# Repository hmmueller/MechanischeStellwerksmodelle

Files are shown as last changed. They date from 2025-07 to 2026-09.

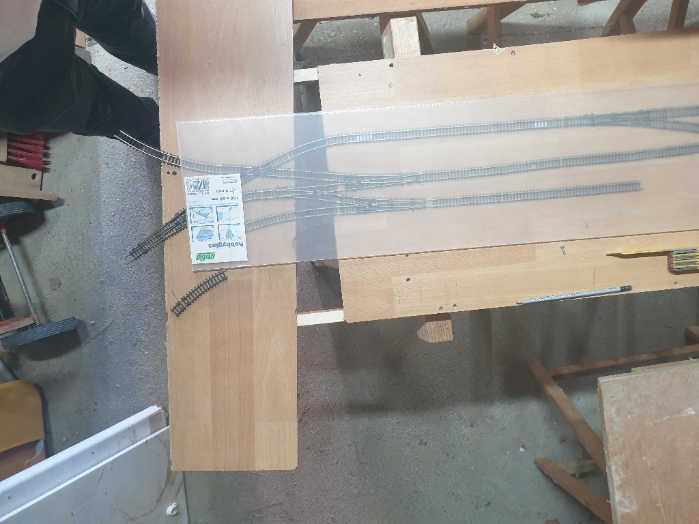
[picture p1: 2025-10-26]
Projektdokumente/20250831.KreuzdorfGleiseAusgelegt.jpeg

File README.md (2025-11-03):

# Mechanische Stellwerksmodelle

Pläne für nachempfundene Mechaniken von Stellwerken

* Die CAD-Dateien (.MOD-Dateien) sind mit BeckerCAD 11 2D gezeichnet.
* Die CNC-Pfad-Zeichnungen (P-, S- und V-Blätter) sind Input für den [PathDxf2GCode-Generator](https://github.com/hmmueller/PathDxf2GCode).

Plans for functional models of mechanical railway interlockings

* The CAD files (.MOD files) are created with BeckerCAD 11 2D.
* The CNC path drawings (P, S and V files) are input for the gcode generator [PathDxf2GCode](https://github.com/hmmueller/PathDxf2GCode).

Shield: [][cc-by]

This work is licensed under a
[Creative Commons Attribution 4.0 International License][cc-by].

[][cc-by]

[cc-by]: http://creativecommons.org/licenses/by/4.0/
[cc-by-image]: https://i.creativecommons.org/l/by/4.0/88x31.png
[cc-by-shield]: https://img.shields.io/badge/License-CC%20BY%204.0-lightgrey.svg

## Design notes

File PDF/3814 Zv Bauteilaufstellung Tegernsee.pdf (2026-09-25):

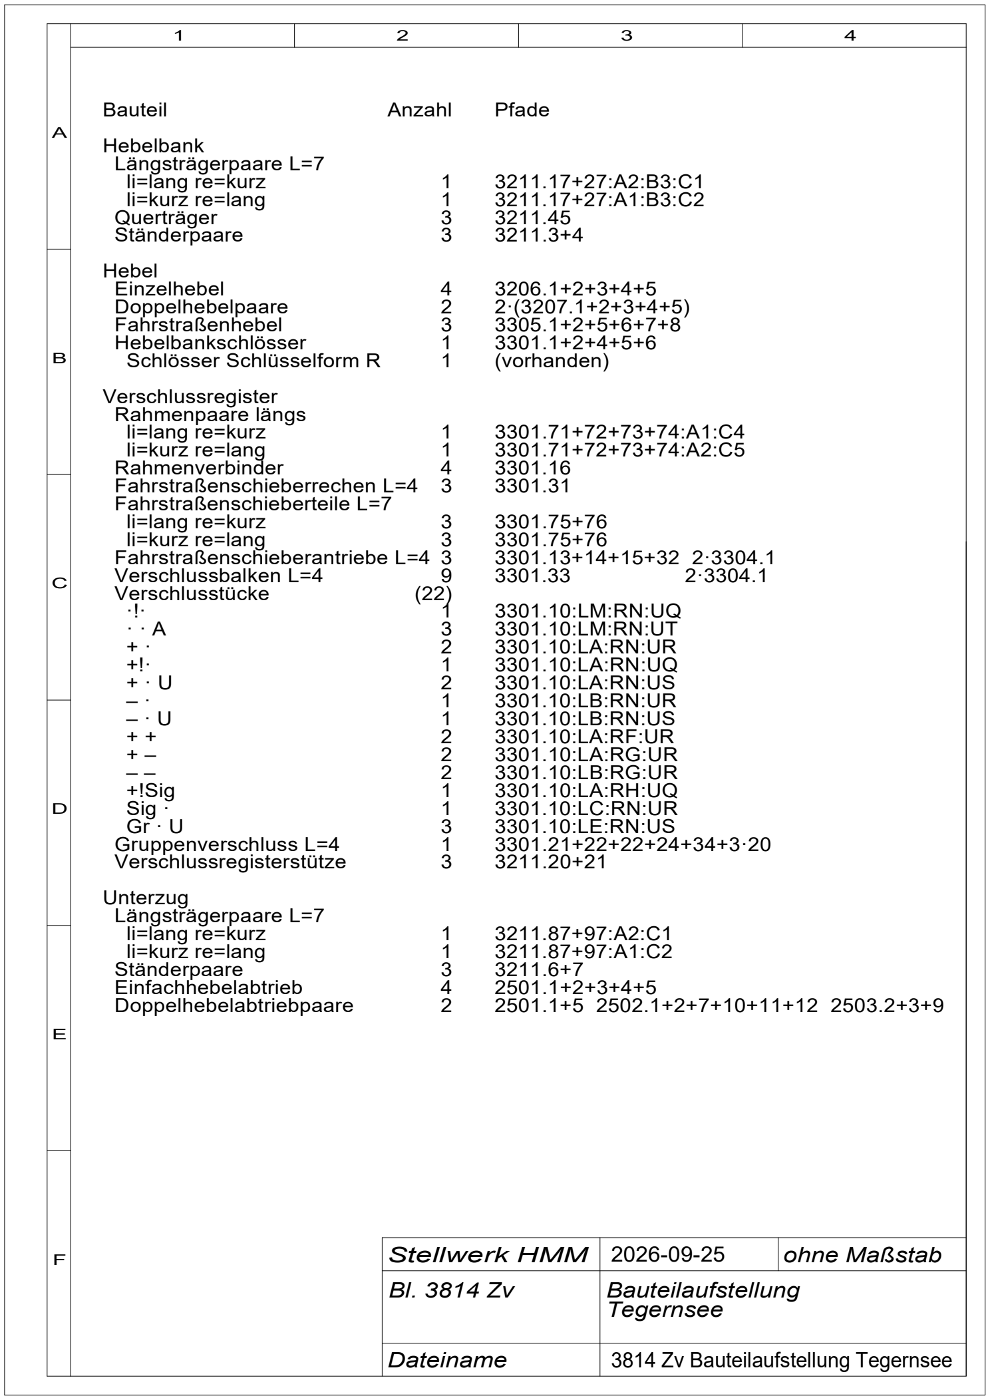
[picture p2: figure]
Stellwerk HMM; ohne Maßstab; Bauteilaufstellung Tegernsee; Dateiname; 3814 Zv Bauteilaufstellung Tegernsee; Pfade; 3206.1+2+3+4+5 2·(3207.1+2+3+4+5) 3305.1+2+5+6+7+8 3301.1+2+4+5+6 (vorhanden); Anzahl; Bauteil; Hebelbank Längsträgerpaare L=7 li=lang re=kurz li=kurz re=lang Querträger Ständerpaare; Hebel Einzelhebel Doppelhebelpaare Fahrstraßenhebel Hebelbankschlösser Schlösser Schlüsselform R; Verschlussregister Rahmenpaare längs li=lang re=kurz li=kurz re=lang Rahmenverbinder Fahrstraßenschieberrechen L=4 Fahrstraßenschieberteile L=7 li=lang re=kurz li=kurz re=lang Fahrstraßenschieberantriebe L=4 Verschlussbalken L=4 Verschlusstücke ·!· · · A + · +!· + · U – · – · U + + + – – – +!Sig Sig · Gr · U Gruppenverschluss L=4 Verschlussregisterstütze; Unterzug Längsträgerpaare L=7 li=lang re=kurz li=kurz re=lang Ständerpaare Einfachhebelabtrieb Doppelhebelabtriebpaare

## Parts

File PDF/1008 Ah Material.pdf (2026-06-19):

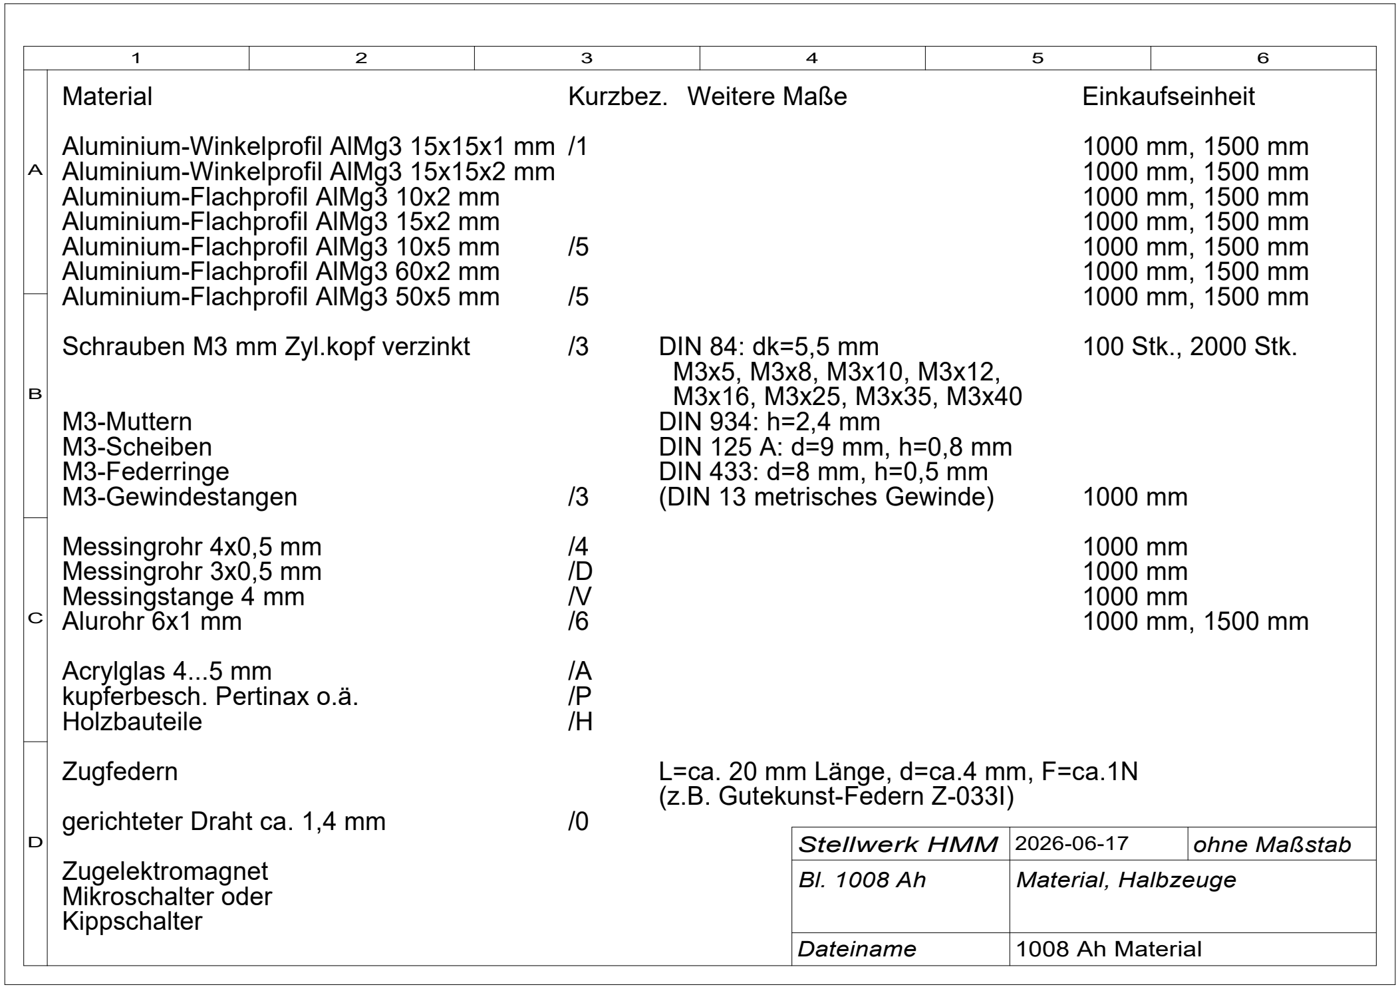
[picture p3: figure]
Stellwerk HMM; ohne Maßstab; Material, Halbzeuge; Dateiname; 1008 Ah Material; Material; Aluminium-Winkelprofil AlMg3 15x15x1 mm Aluminium-Winkelprofil AlMg3 15x15x2 mm Aluminium-Flachprofil AlMg3 10x2 mm Aluminium-Flachprofil AlMg3 15x2 mm Aluminium-Flachprofil AlMg3 10x5 mm Aluminium-Flachprofil AlMg3 60x2 mm Aluminium-Flachprofil AlMg3 50x5 mm; Schrauben M3 mm Zyl.kopf verzinkt; M3-Muttern M3-Scheiben M3-Federringe M3-Gewindestangen; Messingrohr 4x0,5 mm Messingrohr 3x0,5 mm Messingstange 4 mm Alurohr 6x1 mm; Acrylglas 4...5 mm kupferbesch. Pertinax o.ä. Holzbauteile; Zugfedern; gerichteter Draht ca. 1,4 mm; Zugelektromagnet Mikroschalter oder Kippschalter; Weitere Maße; DIN 84: dk=5,5 mm M3x5, M3x8, M3x10, M3x12, M3x16, M3x25, M3x35, M3x40 DIN 934: h=2,4 mm DIN 125 A: d=9 mm, h=0,8 mm DIN 433: d=8 mm, h=0,5 mm (DIN 13 metrisches Gewinde); L=ca. 20 mm Länge, d=ca.4 mm, F=ca.1N (z.B. Gutekunst-Federn Z-033I); Einkaufseinheit; 100 Stk., 2000 Stk.; Kurzbez.

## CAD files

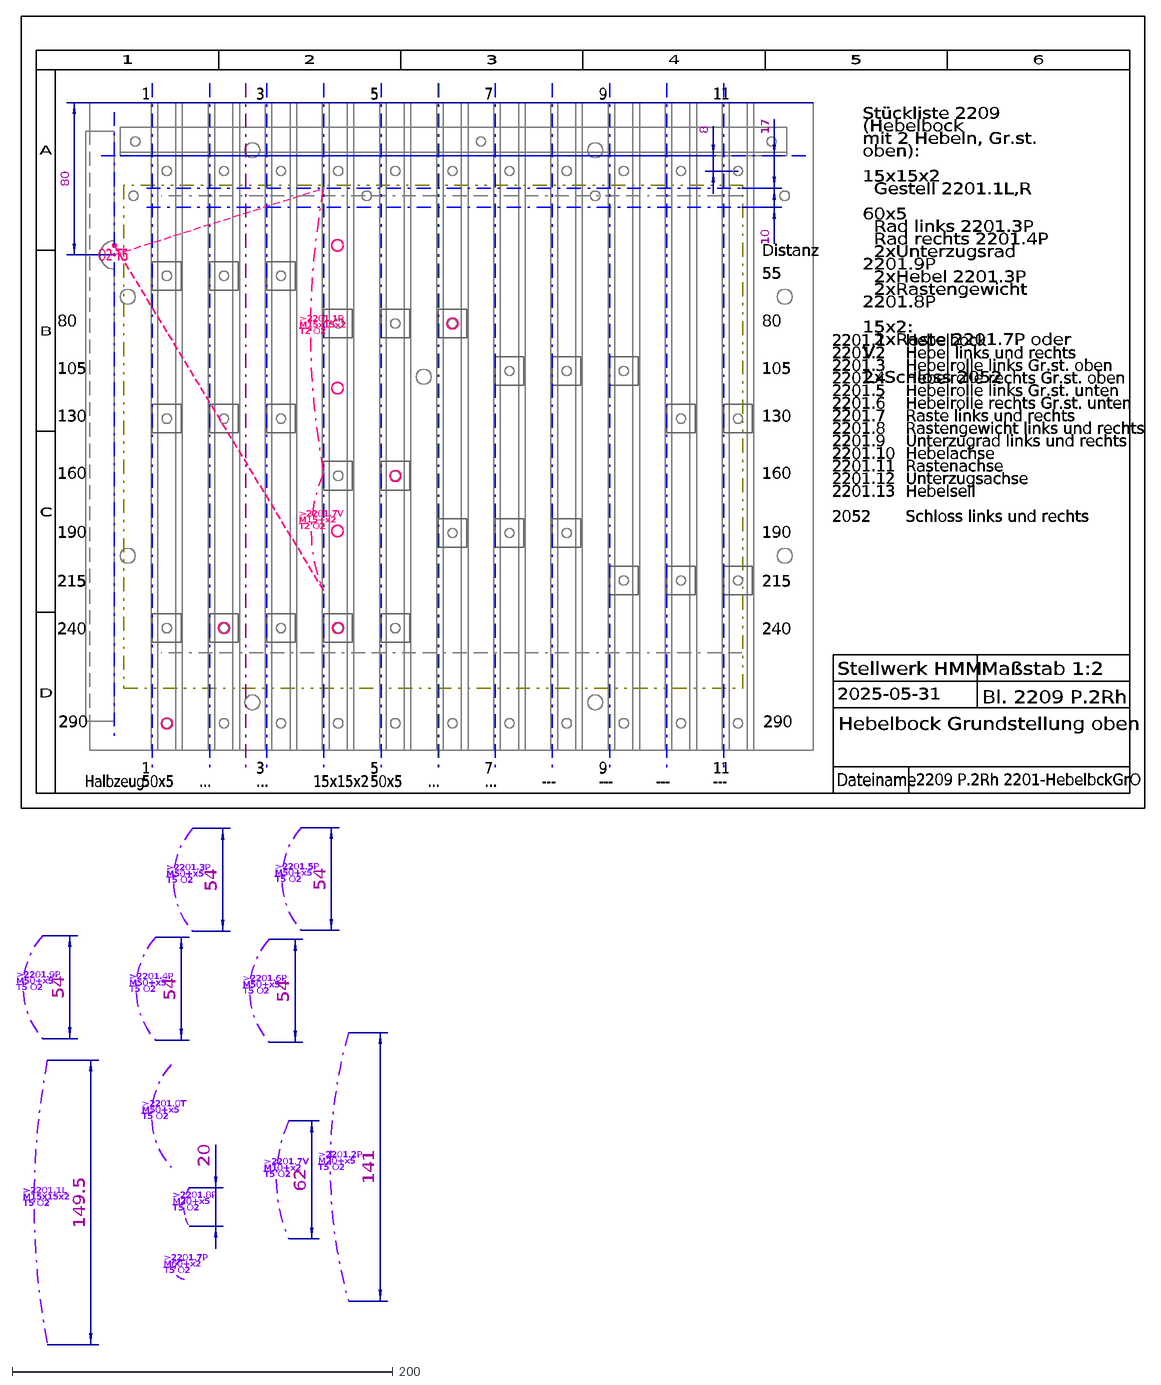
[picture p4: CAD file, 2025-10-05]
Projekte2025/2209 P.2Rh 2201-HebelbckGrO.dxf
80
105
130
190
215
240
290
55
Distanz
8
1
9
7
3
5
11
17
10
160
50x5
...
15x15x2
---
Halbzeug:
Stückliste 2209 (Hebelbock mit 2 Hebeln, Gr.st. oben): 15x15x2 Gestell 2201.1L,R 60x5 Rad links 2201.3P Rad rechts 2201.4P 2xUnterzugsrad 2201.9P 2xHebel 2201.3
>2201.3P M50+x5 T5 O2
>2201.7V M10+x2 T5 O2
>2201.5P M50+x5 T5 O2
>2201.1L M15x15x2 T5 O2
>2201.4P M50+x5 T5 O2
>2201.9P M50+x5 T5 O2
>2201.0T M50+x5 T5 O2
>2201.8P M20+x5 T5 O2
>2201.7P M60+x2 T5 O2
>2201.2P M20+x5 T5 O2
>2201.6P M50+x5 T5 O2
54
149.5
20
62
141
>2201.1R M15x15x2 T2 O2
>2201.7V M15+x2 T2 O2
Hebelbock Hebel links und rechts Hebelrolle links Gr.st. oben Hebelrolle rechts Gr.st. oben Hebelrolle links Gr.st. unten Hebelrolle rechts Gr.st. unten Raste l
2201.1 2201.2 2201.3 2201.4 2201.5 2201.6 2201.7 2201.8 2201.9 2201.10 2201.11 2201.12 2201.13 2052
O2 T5
2209 P.2Rh 2201-HebelbckGrO
2
4
6
A
B
C
D
Hebelbock Grundstellung oben
Bl. 2209 P.2Rh
Maßstab 1:2
2025-05-31
Stellwerk HMM
Dateiname

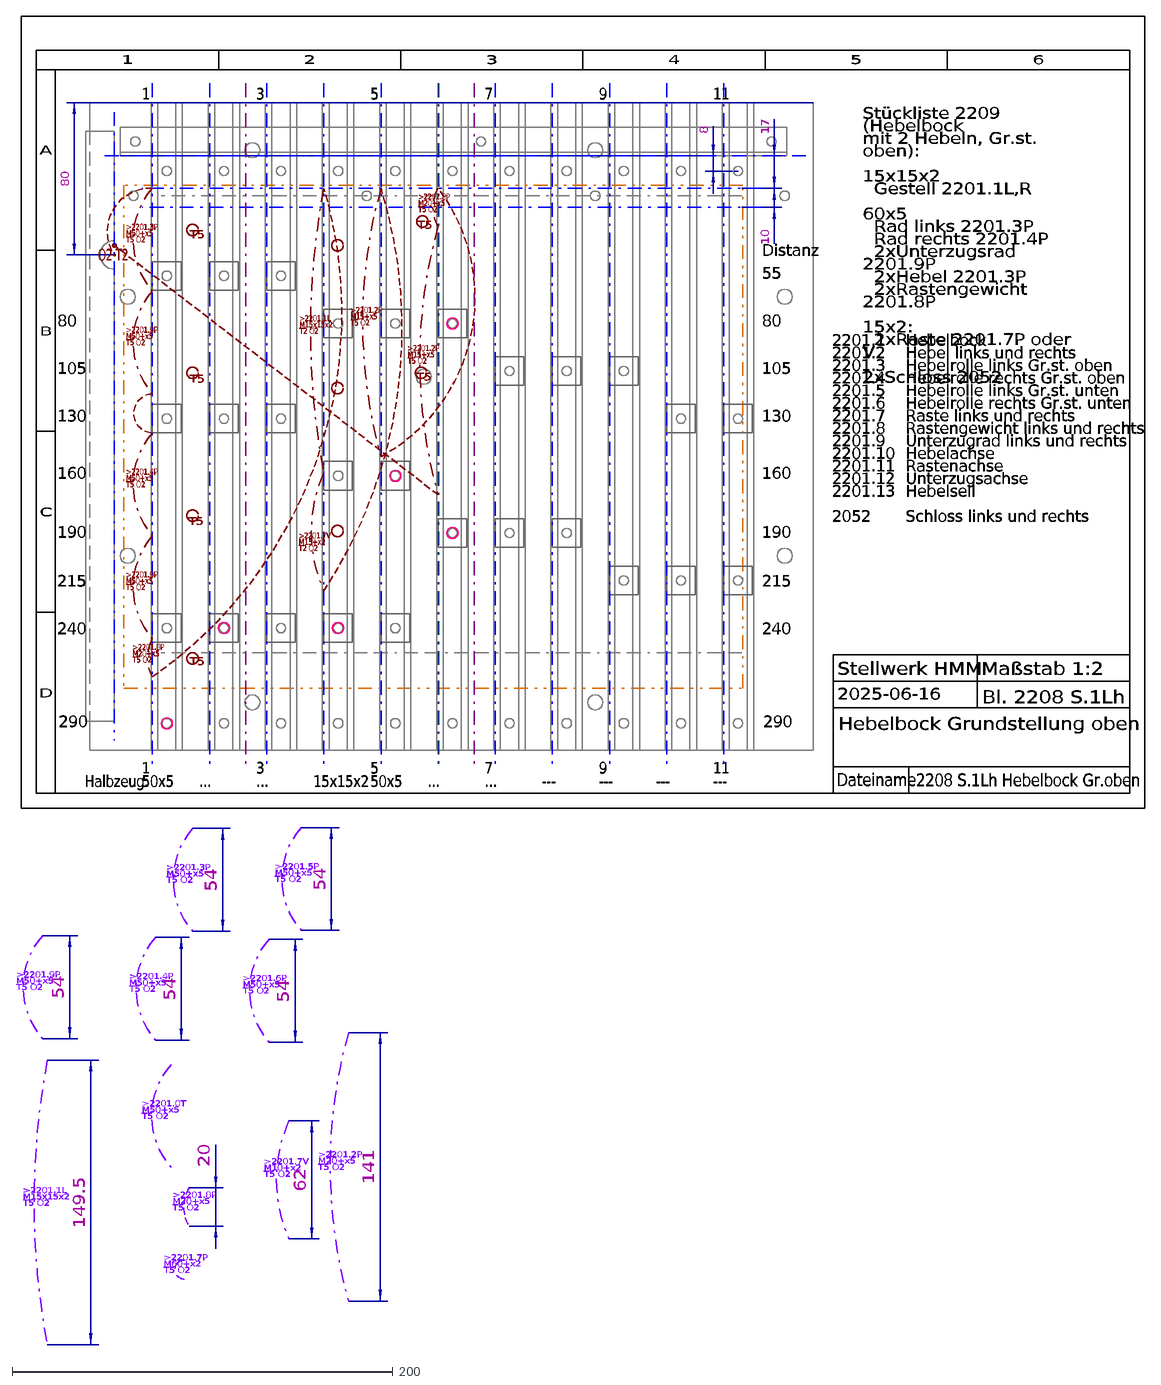
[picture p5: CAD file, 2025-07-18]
Projekte2025/2208 S.1Lh Hebelbock Gr.oben.dxf
80
105
130
190
215
240
290
55
Distanz
8
1
9
7
3
5
11
17
10
160
O2 T2
50x5
...
15x15x2
---
Halbzeug:
Stückliste 2209 (Hebelbock mit 2 Hebeln, Gr.st. oben): 15x15x2 Gestell 2201.1L,R 60x5 Rad links 2201.3P Rad rechts 2201.4P 2xUnterzugsrad 2201.9P 2xHebel 2201.3
>2201.3P M50+x5 T5 O2
>2201.7V M10+x2 T5 O2
>2201.5P M50+x5 T5 O2
>2201.1L M15x15x2 T5 O2
>2201.4P M50+x5 T5 O2
>2201.9P M50+x5 T5 O2
>2201.0T M50+x5 T5 O2
>2201.8P M20+x5 T5 O2
>2201.7P M60+x2 T5 O2
>2201.2P M20+x5 T5 O2
>2201.6P M50+x5 T5 O2
54
149.5
20
62
141
>2201.1L M15x15x2 T2 O2
>2201.7V M15+x2 T2 O2
>2201.2P M15+x5 T5 O2
Hebelbock Hebel links und rechts Hebelrolle links Gr.st. oben Hebelrolle rechts Gr.st. oben Hebelrolle links Gr.st. unten Hebelrolle rechts Gr.st. unten Raste l
2201.1 2201.2 2201.3 2201.4 2201.5 2201.6 2201.7 2201.8 2201.9 2201.10 2201.11 2201.12 2201.13 2052
T5
2208 S.1Lh Hebelbock Gr.oben
2025-06-16
2
4
6
A
B
C
D
Hebelbock Grundstellung oben
Bl. 2208 S.1Lh
Maßstab 1:2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

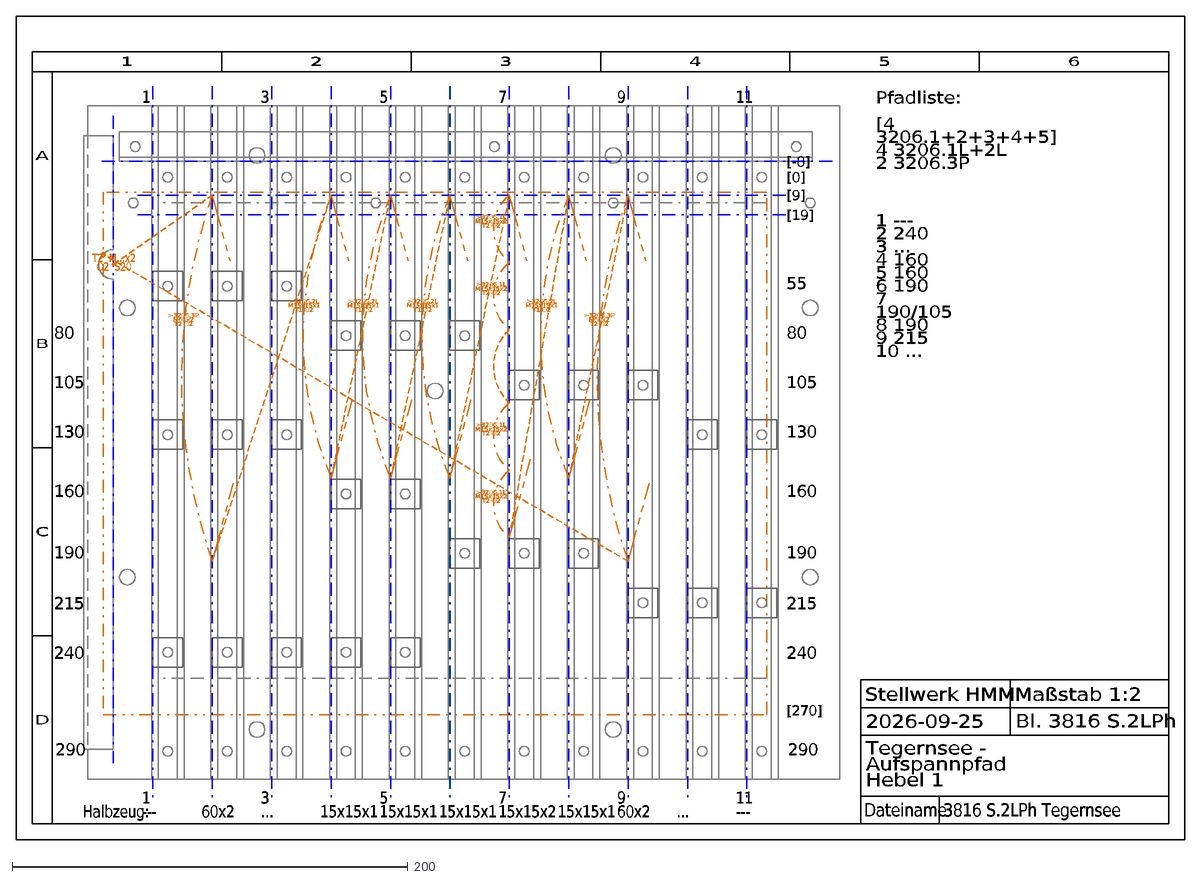
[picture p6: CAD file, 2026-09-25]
DXF2GCode/3816 S.2LPh Tegernsee.dxf
80
105
130
190
215
240
290
55
1
9
7
3
5
11
160
[19]
[9]
[0]
[-8]
[270]
---
60x2
...
15x15x1
15x15x2
Halbzeug:
Pfadliste: [4 3206.1+2+3+4+5] 4 3206.1L+2L 2 3206.3P
2026-09-25
3816 S.2LPh Tegernsee
>3206.2L M15x15x1 T1 O2
>3206.1L M15x15x2 T2 O2
>3206.3P M60x2 T2 O2
T2 M...x2 O2 S20
1 --- 2 240 3 ... 4 160 5 160 6 190 7 190/105 8 190 9 215 10 ...
2
4
6
A
B
C
D
Tegernsee - Aufspannpfad Hebel 1
Bl. 3816 S.2LPh
Maßstab 1:2
Stellwerk HMM
Dateiname

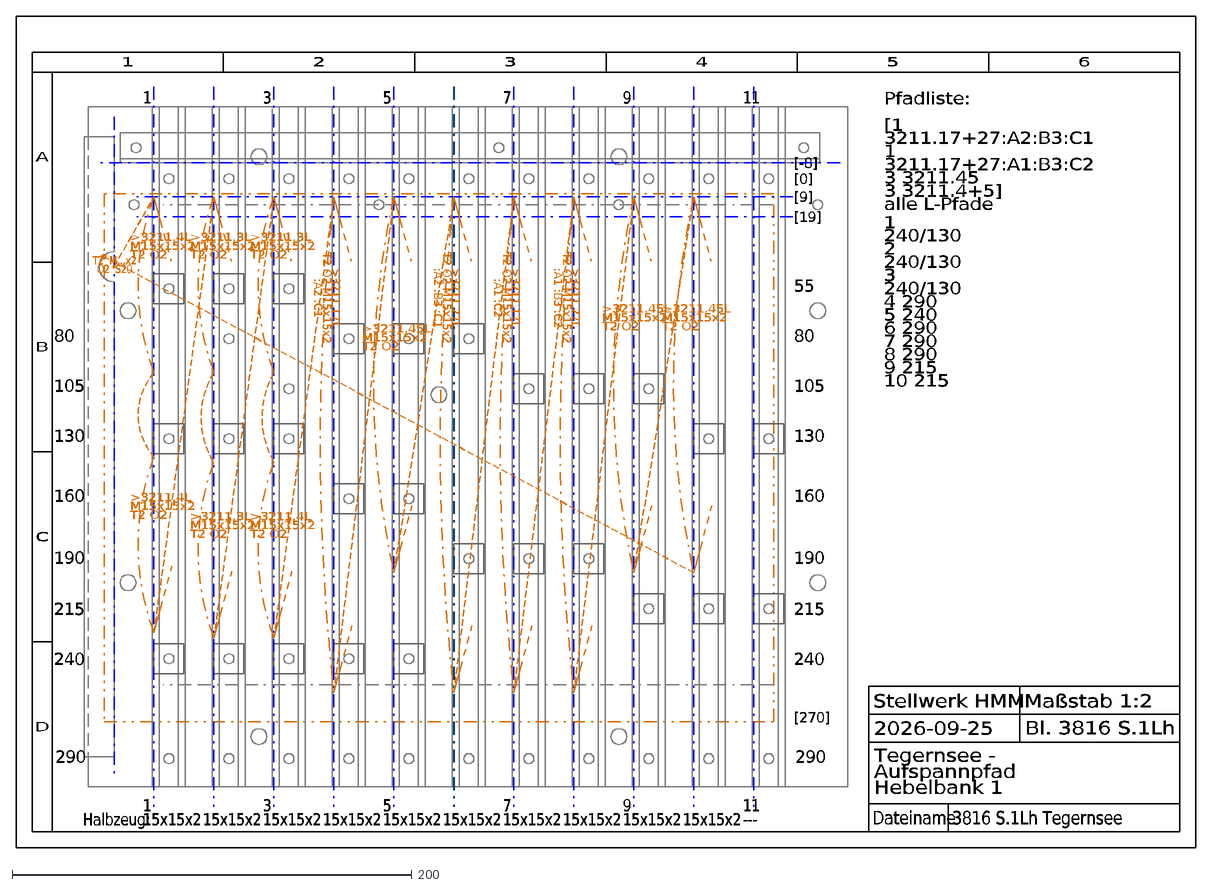
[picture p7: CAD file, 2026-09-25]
DXF2GCode/3816 S.1Lh Tegernsee.dxf
80
105
130
190
215
240
290
55
1
9
7
3
5
11
160
[19]
[9]
[0]
[-8]
[270]
15x15x2
---
Halbzeug:
Pfadliste: [1 3211.17+27:A2:B3:C1 1 3211.17+27:A1:B3:C2 3 3211.45 3 3211.4+5] alle L-Pfade
2026-09-25
3816 S.1Lh Tegernsee
T2 M...x2 O2 S20
>3211.17L T2 O2 M15x15x2 :A2 :C1
>3211.27L T2 O2 M15x15x2 :A2 :B3 :C1
>3211.27L T2 O2 M15x15x2 :A1 :B3 :C2
>3211.17L T2 O2 M15x15x2 :A1 :C2
>3211.45L M15x15x2 T2 O2
>3211.3L M15x15x2 T2 O2
>3211.4L M15x15x2 T2 O2
1 240/130 2 240/130 3 240/130 4 290 5 240 6 290 7 290 8 290 9 215 10 215
2
4
6
A
B
C
D
Tegernsee - Aufspannpfad Hebelbank 1
Bl. 3816 S.1Lh
Maßstab 1:2
Stellwerk HMM
Dateiname

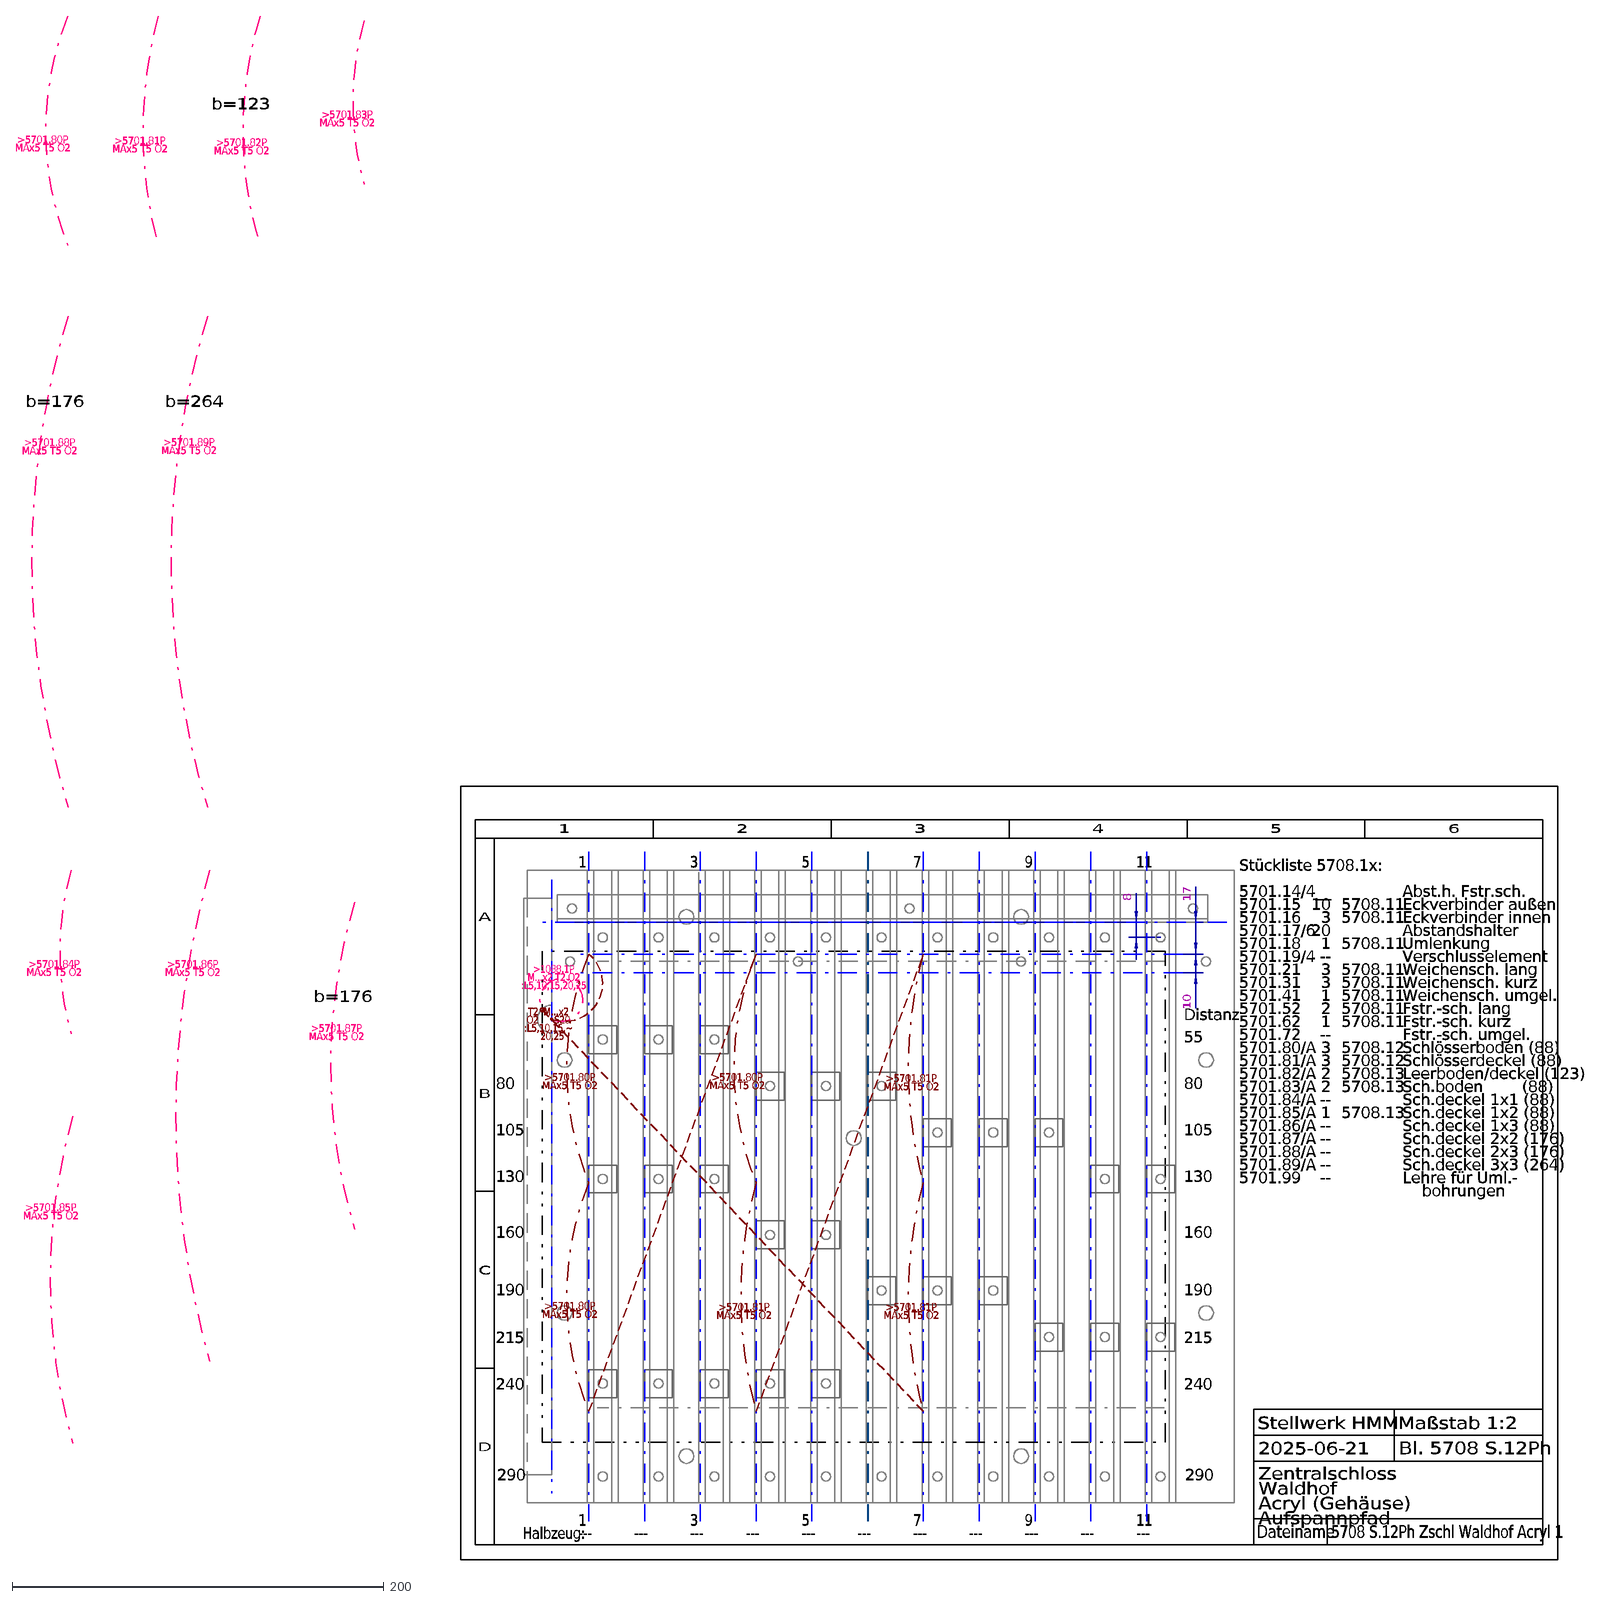
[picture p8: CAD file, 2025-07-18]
Projekte2025/5708 S.12Ph Zschl Waldhof Acryl 1.dxf
80
105
130
190
215
240
290
55
Distanz
8
1
9
7
3
5
11
17
10
160
---
Halbzeug:
2025-06-21
5708 S.12Ph Zschl Waldhof Acryl 1
>1088.1P M...x2 T2 O2 :L5,10,15,20,25
T2 M...x2 O2 S20 :L5,10,15,~ 20,25
5708.11 5708.11 5708.11 5708.11 5708.11 5708.11 5708.11 5708.11 5708.12 5708.12 5708.13 5708.13 5708.13
Abst.h. Fstr.sch. Eckverbinder außen Eckverbinder innen Abstandshalter Umlenkung Verschlusselement Weichensch. lang Weichensch. kurz Weichensch. umgel. Fstr.-sc
Stückliste 5708.1x: 5701.14/4 5701.15 5701.16 5701.17/6 5701.18 5701.19/4 5701.21 5701.31 5701.41 5701.52 5701.62 5701.72 5701.80/A 5701.81/A 5701.82/A 5701.83/
__ 10 3 20 1 -- 3 3 1 2 1 -- 3 3 2 2 -- 1 -- -- -- -- --
>5701.80P MAx5 T5 O2
>5701.81P MAx5 T5 O2
b=176
b=264
b=123
>5701.85P MAx5 T5 O2
>5701.84P MAx5 T5 O2
>5701.88P MAx5 T5 O2
>5701.82P MAx5 T5 O2
>5701.86P MAx5 T5 O2
>5701.83P MAx5 T5 O2
>5701.87P MAx5 T5 O2
>5701.89P MAx5 T5 O2
2
4
6
A
B
C
D
Zentralschloss Waldhof Acryl (Gehäuse) Aufspannpfad
Bl. 5708 S.12Ph
Maßstab 1:2
Stellwerk HMM
Dateiname

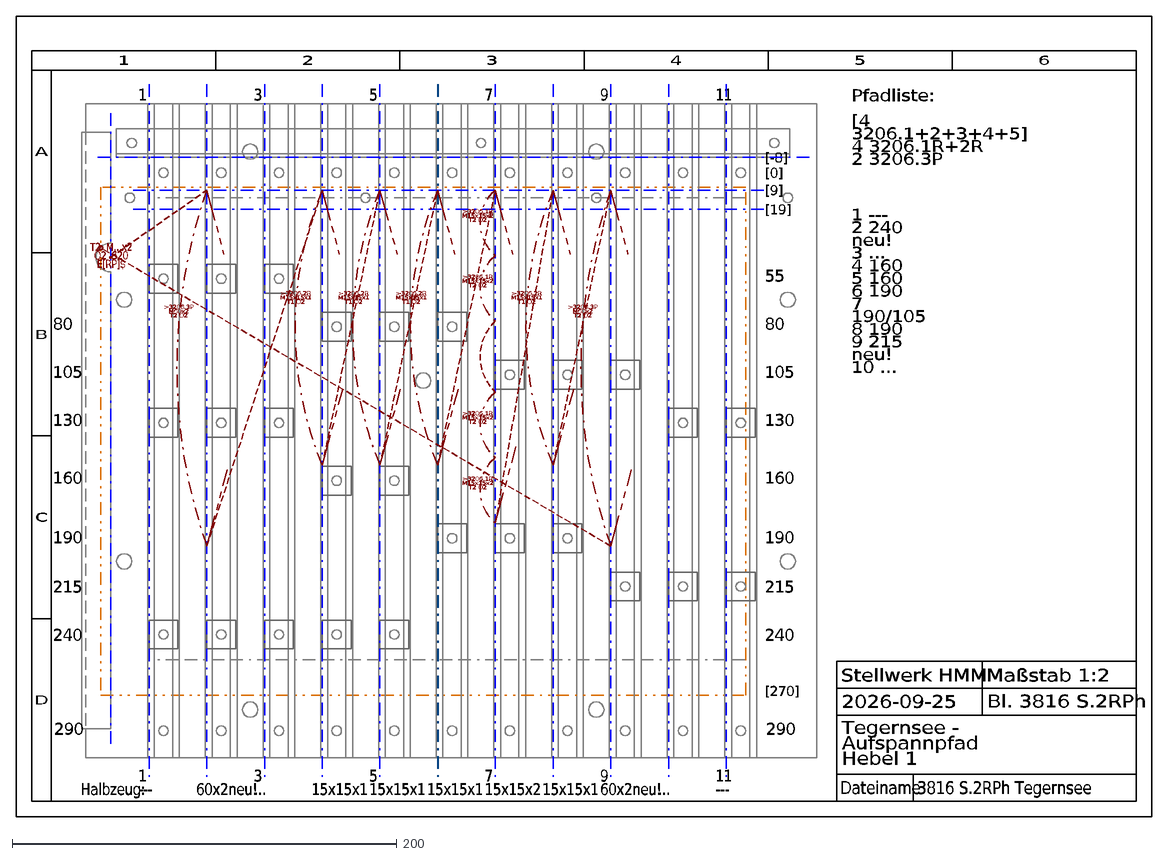
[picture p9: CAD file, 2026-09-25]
DXF2GCode/3816 S.2RPh Tegernsee.dxf
80
105
130
190
215
240
290
55
1
9
7
3
5
11
160
[19]
[9]
[0]
[-8]
[270]
---
60x2neu!
...
15x15x1
15x15x2
Halbzeug:
Pfadliste: [4 3206.1+2+3+4+5] 4 3206.1R+2R 2 3206.3P
2026-09-25
3816 S.2RPh Tegernsee
>3206.2R M15x15x1 T1 O2
>3206.1R M15x15x2 T2 O2
>3206.3P M60x2 T2 O2
T2 M...x2 O2 S20 E[RP]$
1 --- 2 240 neu! 3 ... 4 160 5 160 6 190 7 190/105 8 190 9 215 neu! 10 ...
2
4
6
A
B
C
D
Tegernsee - Aufspannpfad Hebel 1
Bl. 3816 S.2RPh
Maßstab 1:2
Stellwerk HMM
Dateiname

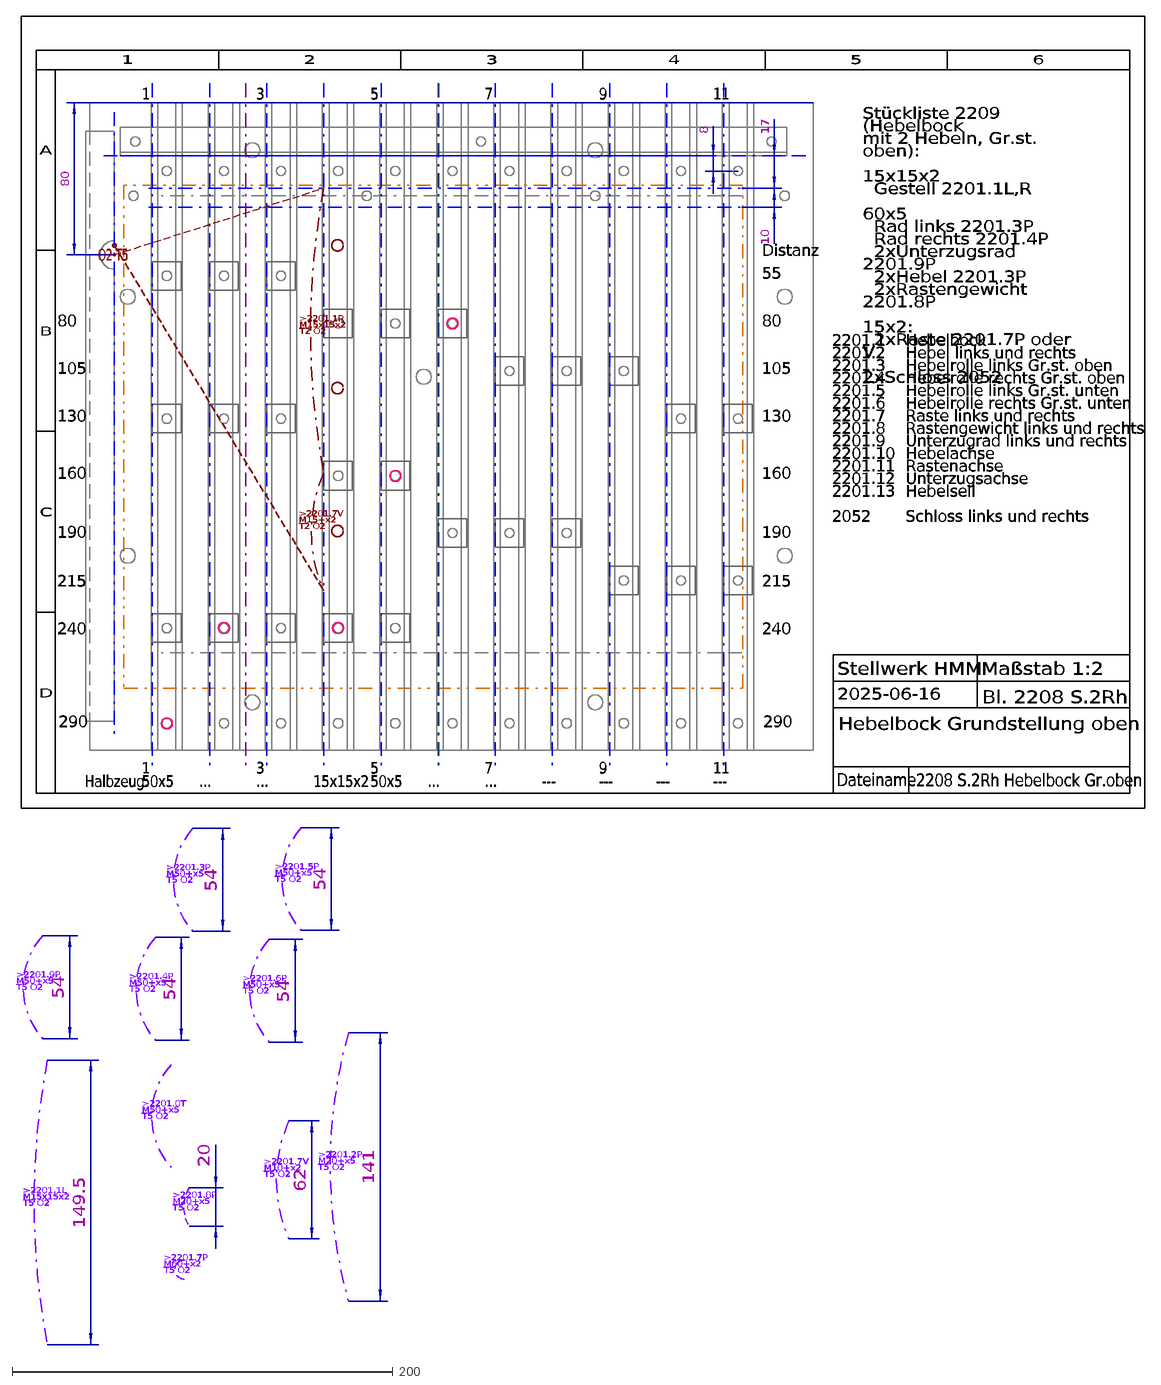
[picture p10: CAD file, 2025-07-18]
Projekte2025/2208 S.2Rh Hebelbock Gr.oben.dxf
80
105
130
190
215
240
290
55
Distanz
8
1
9
7
3
5
11
17
10
160
50x5
...
15x15x2
---
Halbzeug:
Stückliste 2209 (Hebelbock mit 2 Hebeln, Gr.st. oben): 15x15x2 Gestell 2201.1L,R 60x5 Rad links 2201.3P Rad rechts 2201.4P 2xUnterzugsrad 2201.9P 2xHebel 2201.3
>2201.3P M50+x5 T5 O2
>2201.7V M10+x2 T5 O2
>2201.5P M50+x5 T5 O2
>2201.1L M15x15x2 T5 O2
>2201.4P M50+x5 T5 O2
>2201.9P M50+x5 T5 O2
>2201.0T M50+x5 T5 O2
>2201.8P M20+x5 T5 O2
>2201.7P M60+x2 T5 O2
>2201.2P M20+x5 T5 O2
>2201.6P M50+x5 T5 O2
54
149.5
20
62
141
>2201.1R M15x15x2 T2 O2
>2201.7V M15+x2 T2 O2
Hebelbock Hebel links und rechts Hebelrolle links Gr.st. oben Hebelrolle rechts Gr.st. oben Hebelrolle links Gr.st. unten Hebelrolle rechts Gr.st. unten Raste l
2201.1 2201.2 2201.3 2201.4 2201.5 2201.6 2201.7 2201.8 2201.9 2201.10 2201.11 2201.12 2201.13 2052
O2 T5
2208 S.2Rh Hebelbock Gr.oben
2025-06-16
2
4
6
A
B
C
D
Hebelbock Grundstellung oben
Bl. 2208 S.2Rh
Maßstab 1:2
Stellwerk HMM
Dateiname

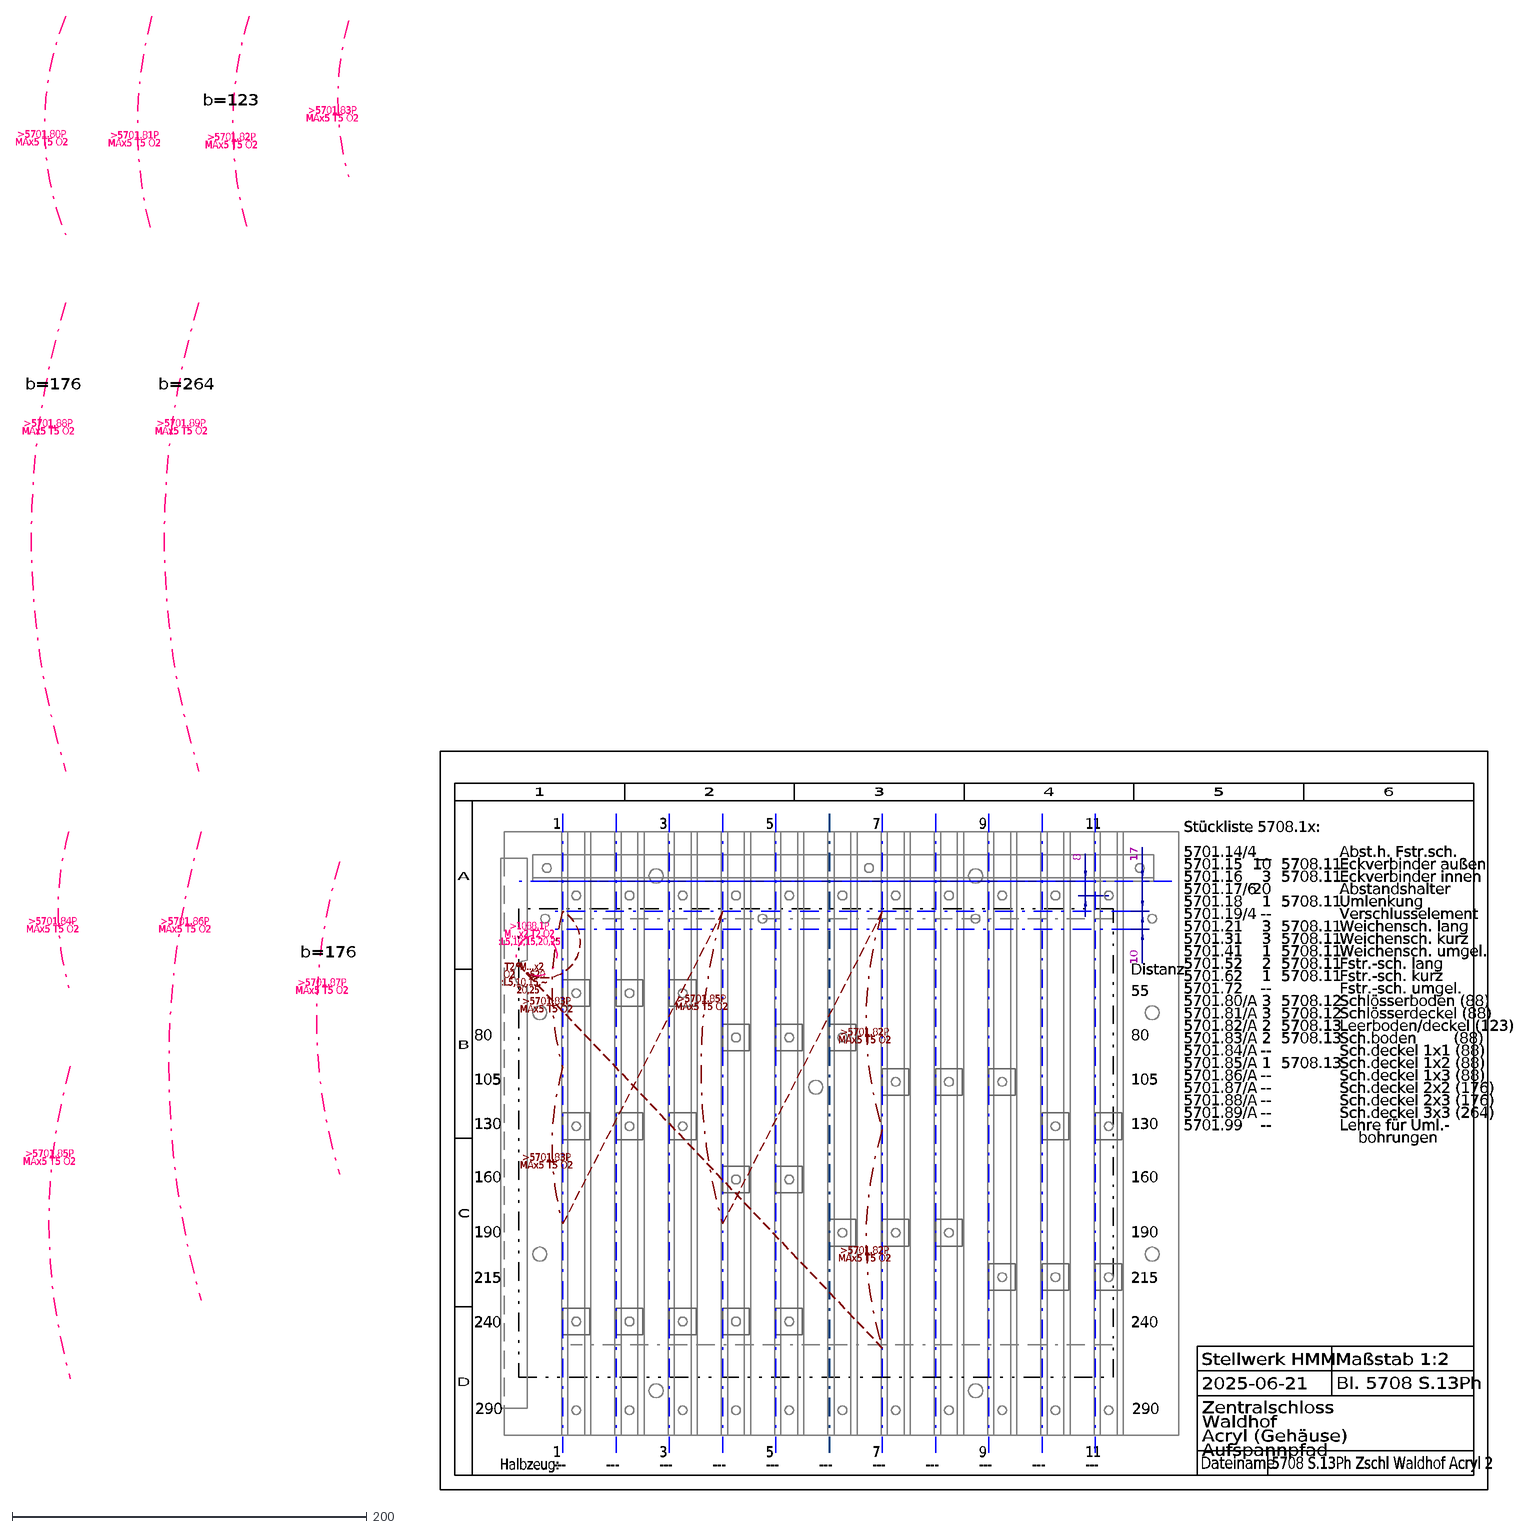
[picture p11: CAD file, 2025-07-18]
Projekte2025/5708 S.13Ph Zschl Waldhof Acryl 2.dxf
80
105
130
190
215
240
290
55
Distanz
8
1
9
7
3
5
11
17
10
160
---
Halbzeug:
2025-06-21
5708 S.13Ph Zschl Waldhof Acryl 2
>1088.1P M...x2 T2 O2 :L5,10,15,20,25
T2 M...x2 O2 S20 :L5,10,15,~ 20,25
5708.11 5708.11 5708.11 5708.11 5708.11 5708.11 5708.11 5708.11 5708.12 5708.12 5708.13 5708.13 5708.13
Abst.h. Fstr.sch. Eckverbinder außen Eckverbinder innen Abstandshalter Umlenkung Verschlusselement Weichensch. lang Weichensch. kurz Weichensch. umgel. Fstr.-sc
Stückliste 5708.1x: 5701.14/4 5701.15 5701.16 5701.17/6 5701.18 5701.19/4 5701.21 5701.31 5701.41 5701.52 5701.62 5701.72 5701.80/A 5701.81/A 5701.82/A 5701.83/
__ 10 3 20 1 -- 3 3 1 2 1 -- 3 3 2 2 -- 1 -- -- -- -- --
b=176
b=264
>5701.81P MAx5 T5 O2
b=123
>5701.85P MAx5 T5 O2
>5701.88P MAx5 T5 O2
>5701.80P MAx5 T5 O2
>5701.82P MAx5 T5 O2
>5701.84P MAx5 T5 O2
>5701.89P MAx5 T5 O2
>5701.83P MAx5 T5 O2
>5701.87P MAx5 T5 O2
>5701.86P MAx5 T5 O2
2
4
6
A
B
C
D
Zentralschloss Waldhof Acryl (Gehäuse) Aufspannpfad
Bl. 5708 S.13Ph
Maßstab 1:2
Stellwerk HMM
Dateiname

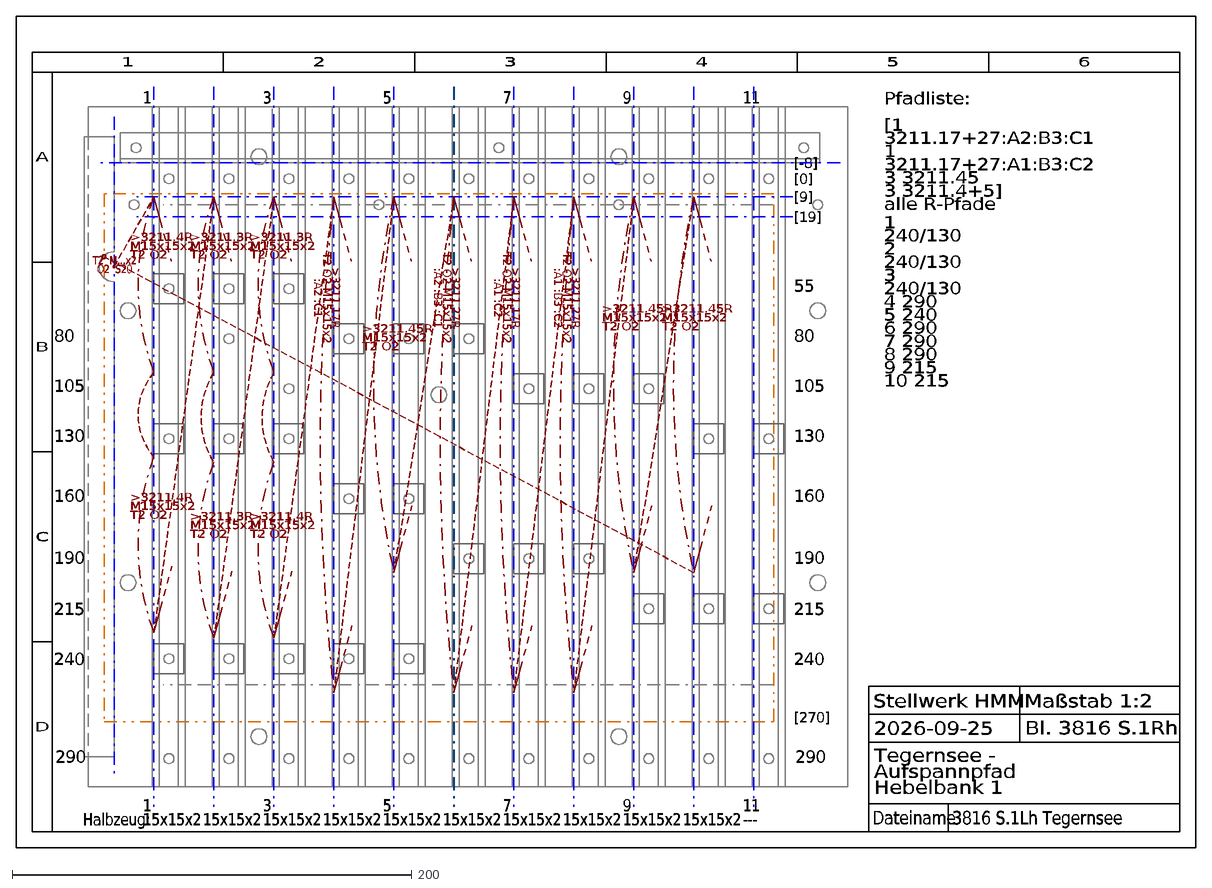
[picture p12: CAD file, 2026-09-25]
DXF2GCode/3816 S.1Rh Tegernsee.dxf
80
105
130
190
215
240
290
55
1
9
7
3
5
11
160
[19]
[9]
[0]
[-8]
[270]
15x15x2
---
Halbzeug:
Pfadliste: [1 3211.17+27:A2:B3:C1 1 3211.17+27:A1:B3:C2 3 3211.45 3 3211.4+5] alle R-Pfade
2026-09-25
3816 S.1Lh Tegernsee
T2 M...x2 O2 S20
>3211.17R T2 O2 M15x15x2 :A2 :C1
>3211.27R T2 O2 M15x15x2 :A2 :B3 :C1
>3211.27R T2 O2 M15x15x2 :A1 :B3 :C2
>3211.17R T2 O2 M15x15x2 :A1 :C2
>3211.45R M15x15x2 T2 O2
>3211.3R M15x15x2 T2 O2
>3211.4R M15x15x2 T2 O2
1 240/130 2 240/130 3 240/130 4 290 5 240 6 290 7 290 8 290 9 215 10 215
2
4
6
A
B
C
D
Tegernsee - Aufspannpfad Hebelbank 1
Bl. 3816 S.1Rh
Maßstab 1:2
Stellwerk HMM
Dateiname

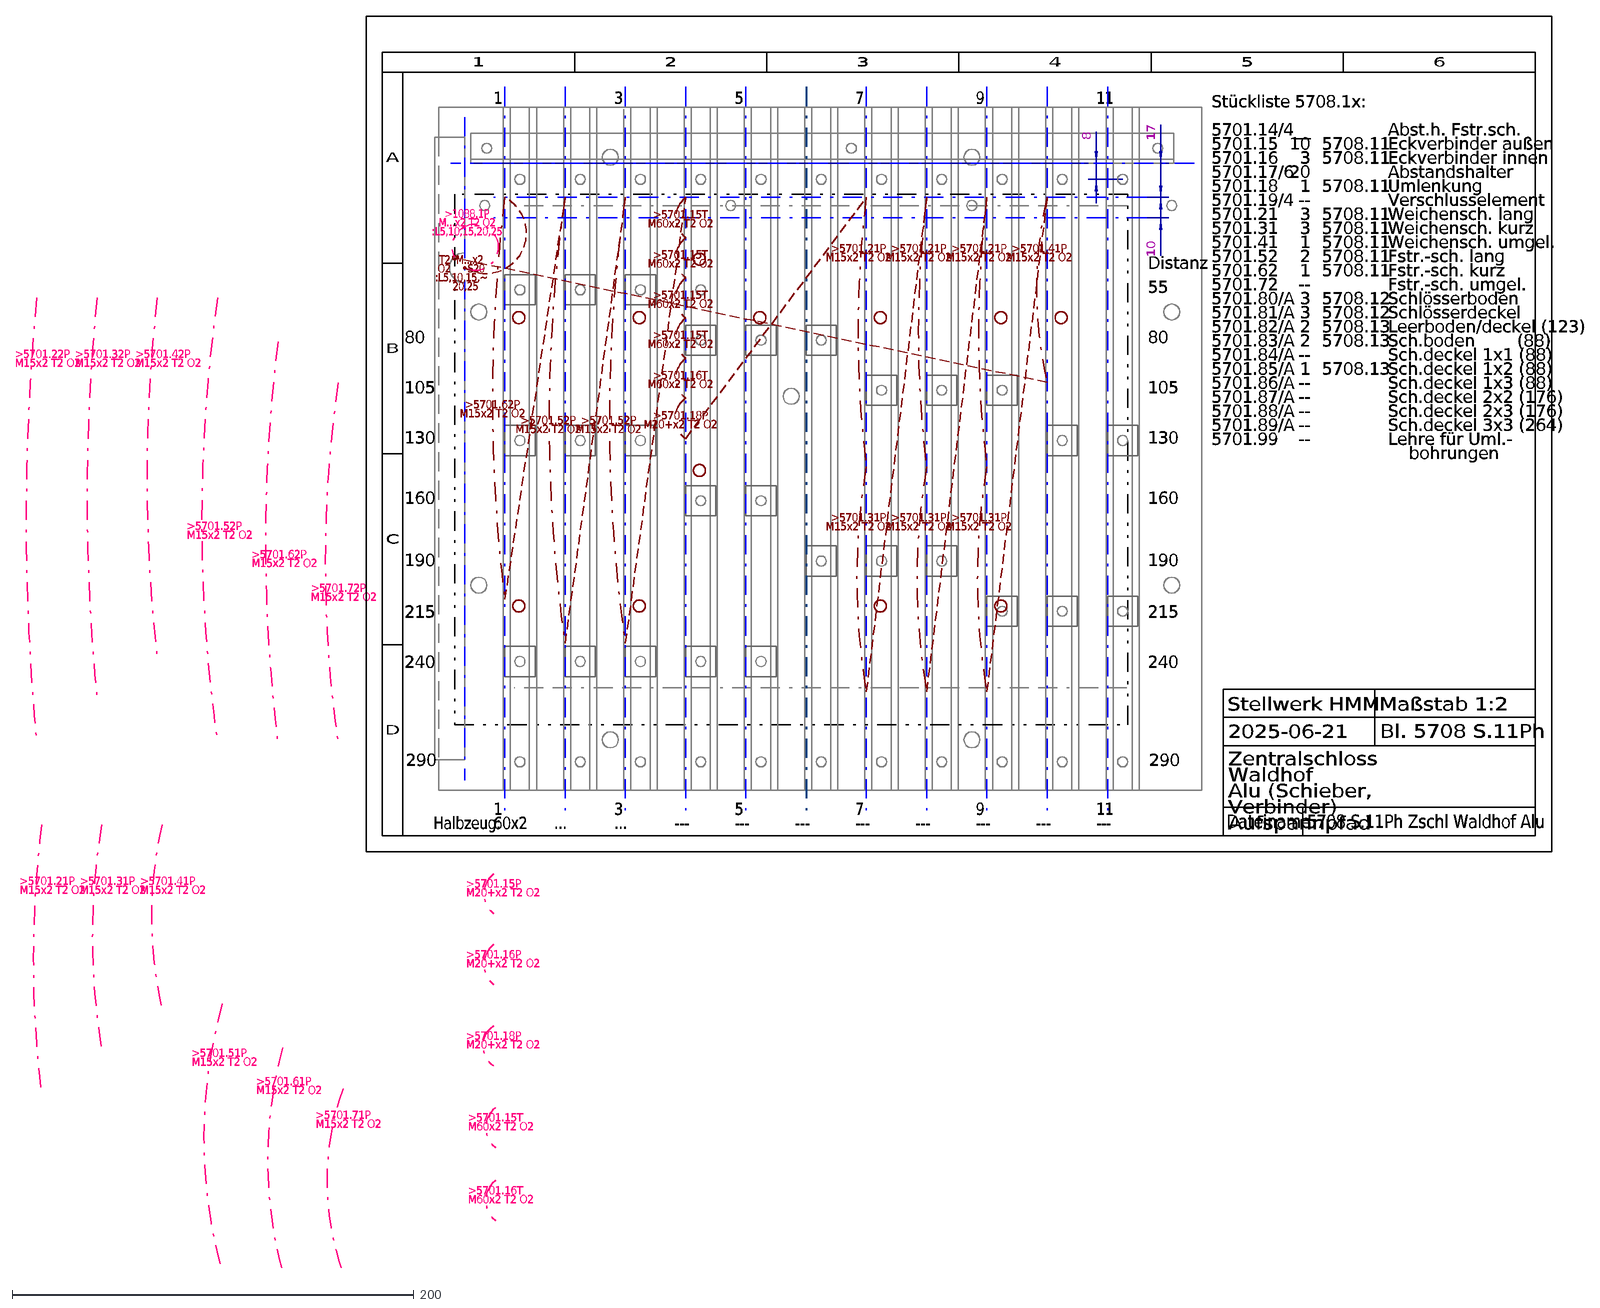
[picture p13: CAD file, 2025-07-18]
Projekte2025/5708 S.11Ph Zschl Waldhof Alu.dxf
80
105
130
190
215
240
290
55
Distanz
8
1
9
7
3
5
11
17
10
160
60x2
...
---
Halbzeug:
2025-06-21
5708 S.11Ph Zschl Waldhof Alu
>1088.1P M...x2 T2 O2 :L5,10,15,20,25
T2 M...x2 O2 S20 :L5,10,15,~ 20,25
Abst.h. Fstr.sch. Eckverbinder außen Eckverbinder innen Abstandshalter Umlenkung Verschlusselement Weichensch. lang Weichensch. kurz Weichensch. umgel. Fstr.-sc
Stückliste 5708.1x: 5701.14/4 5701.15 5701.16 5701.17/6 5701.18 5701.19/4 5701.21 5701.31 5701.41 5701.52 5701.62 5701.72 5701.80/A 5701.81/A 5701.82/A 5701.83/
__ 10 3 20 1 -- 3 3 1 2 1 -- 3 3 2 2 -- 1 -- -- -- -- --
>5701.15P M20+x2 T2 O2
>5701.16T M60x2 T2 O2
>5701.16P M20+x2 T2 O2
>5701.18P M20+x2 T2 O2
>5701.15T M60x2 T2 O2
>5701.61P M15x2 T2 O2
>5701.71P M15x2 T2 O2
>5701.51P M15x2 T2 O2
>5701.41P M15x2 T2 O2
>5701.31P M15x2 T2 O2
>5701.21P M15x2 T2 O2
>5701.32P M15x2 T2 O2
>5701.52P M15x2 T2 O2
>5701.62P M15x2 T2 O2
>5701.72P M15x2 T2 O2
>5701.42P M15x2 T2 O2
>5701.22P M15x2 T2 O2
5708.11 5708.11 5708.11 5708.11 5708.11 5708.11 5708.11 5708.11 5708.12 5708.12 5708.13 5708.13 5708.13
2
4
6
A
B
C
D
Zentralschloss Waldhof Alu (Schieber, Verbinder) Aufspannpfad
Bl. 5708 S.11Ph
Maßstab 1:2
Stellwerk HMM
Dateiname

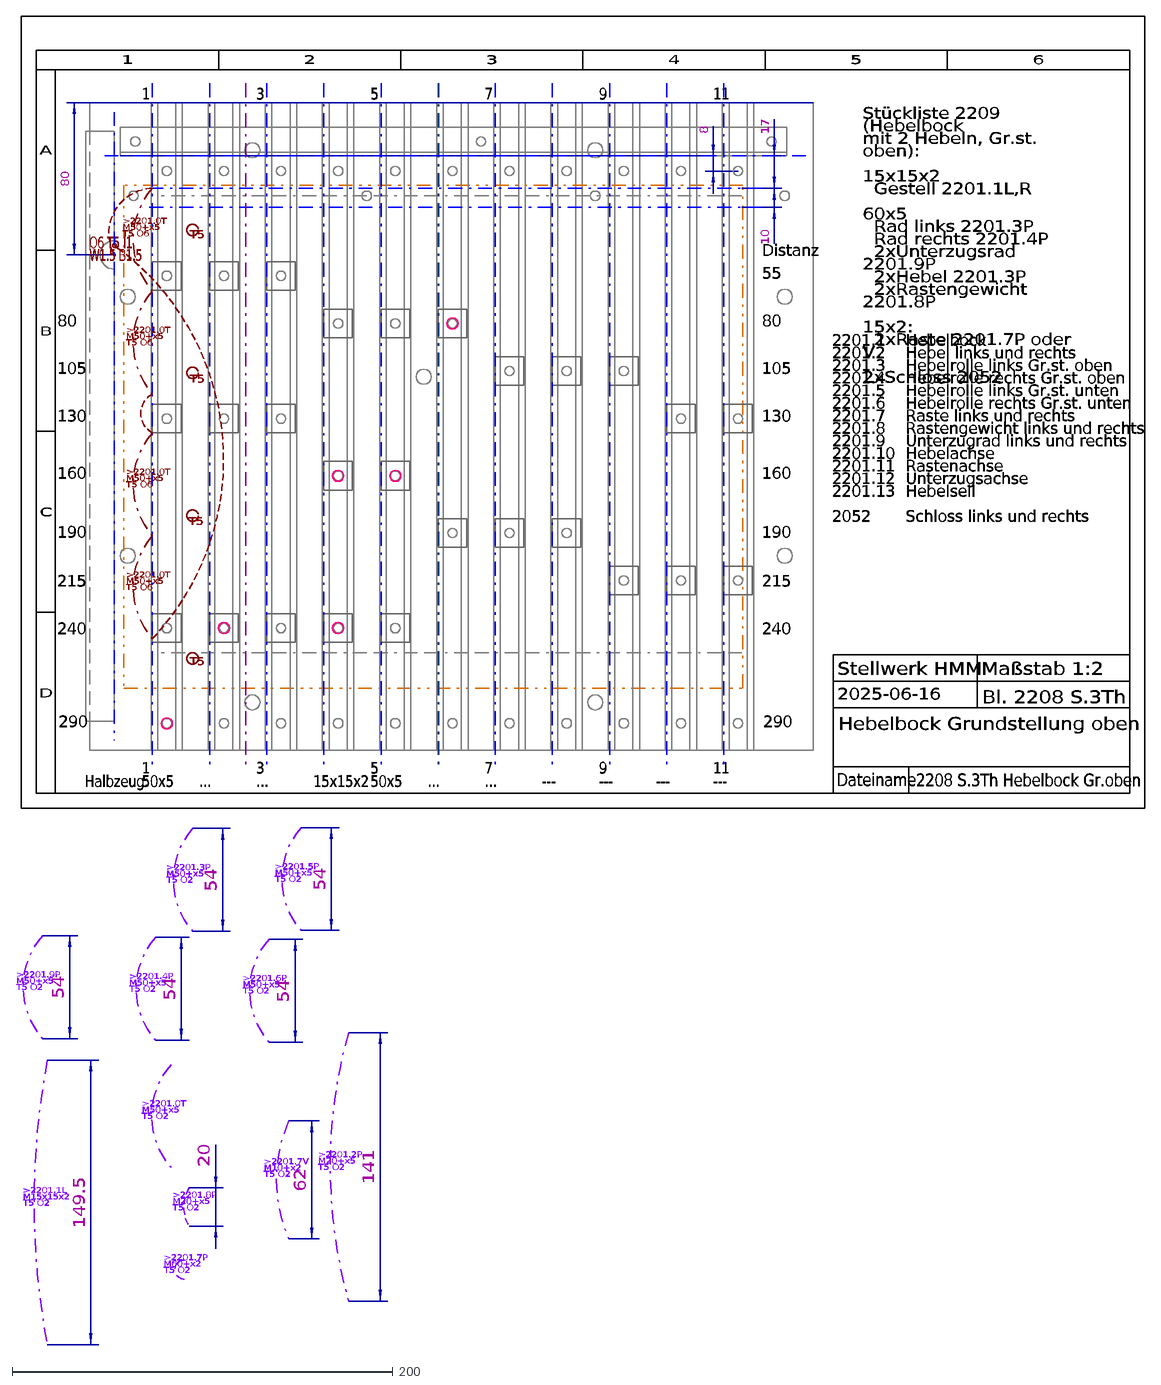
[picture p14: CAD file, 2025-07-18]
Projekte2025/2208 S.3Th Hebelbock Gr.oben.dxf
80
105
130
190
215
240
290
55
Distanz
8
1
9
7
3
5
11
17
10
160
O6 T5 I1 W1.5 B1.5
50x5
...
15x15x2
---
Halbzeug:
Stückliste 2209 (Hebelbock mit 2 Hebeln, Gr.st. oben): 15x15x2 Gestell 2201.1L,R 60x5 Rad links 2201.3P Rad rechts 2201.4P 2xUnterzugsrad 2201.9P 2xHebel 2201.3
>2201.3P M50+x5 T5 O2
>2201.7V M10+x2 T5 O2
>2201.5P M50+x5 T5 O2
>2201.1L M15x15x2 T5 O2
>2201.4P M50+x5 T5 O2
>2201.9P M50+x5 T5 O2
>2201.0T M50+x5 T5 O2
>2201.8P M20+x5 T5 O2
>2201.7P M60+x2 T5 O2
>2201.2P M20+x5 T5 O2
>2201.6P M50+x5 T5 O2
54
149.5
20
62
141
>2201.0T M50+x5 T5 O6
Hebelbock Hebel links und rechts Hebelrolle links Gr.st. oben Hebelrolle rechts Gr.st. oben Hebelrolle links Gr.st. unten Hebelrolle rechts Gr.st. unten Raste l
2201.1 2201.2 2201.3 2201.4 2201.5 2201.6 2201.7 2201.8 2201.9 2201.10 2201.11 2201.12 2201.13 2052
T5
2208 S.3Th Hebelbock Gr.oben
2025-06-16
2
4
6
A
B
C
D
Hebelbock Grundstellung oben
Bl. 2208 S.3Th
Maßstab 1:2
Stellwerk HMM
Dateiname

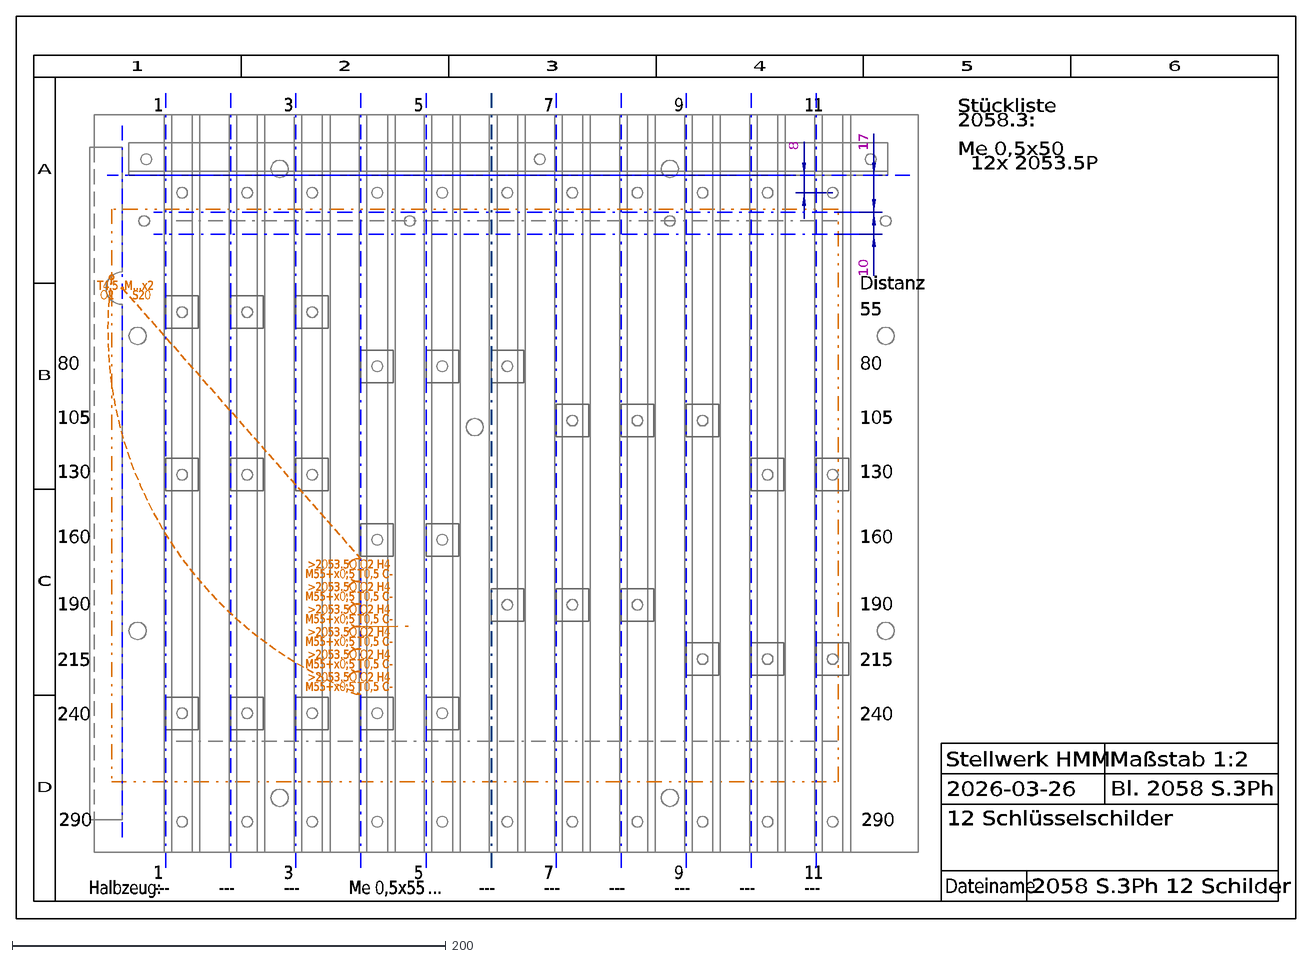
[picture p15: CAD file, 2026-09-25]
DXF2GCode/2058 S.3Ph 12 Schilder.dxf
80
105
130
190
215
240
290
55
Distanz
8
1
9
7
3
5
11
17
10
160
---
Me 0,5x55
...
Halbzeug:
Stückliste 2058.3: Me 0,5x50 12x 2053.5P
2026-03-26
2058 S.3Ph 12 Schilder
T4,5 M...x2 O2 S20
>2053.5Q O2 H4 M55+x0,5 T0,5 C-
2
4
6
A
B
C
D
12 Schlüsselschilder
Bl. 2058 S.3Ph
Maßstab 1:2
Stellwerk HMM
Dateiname

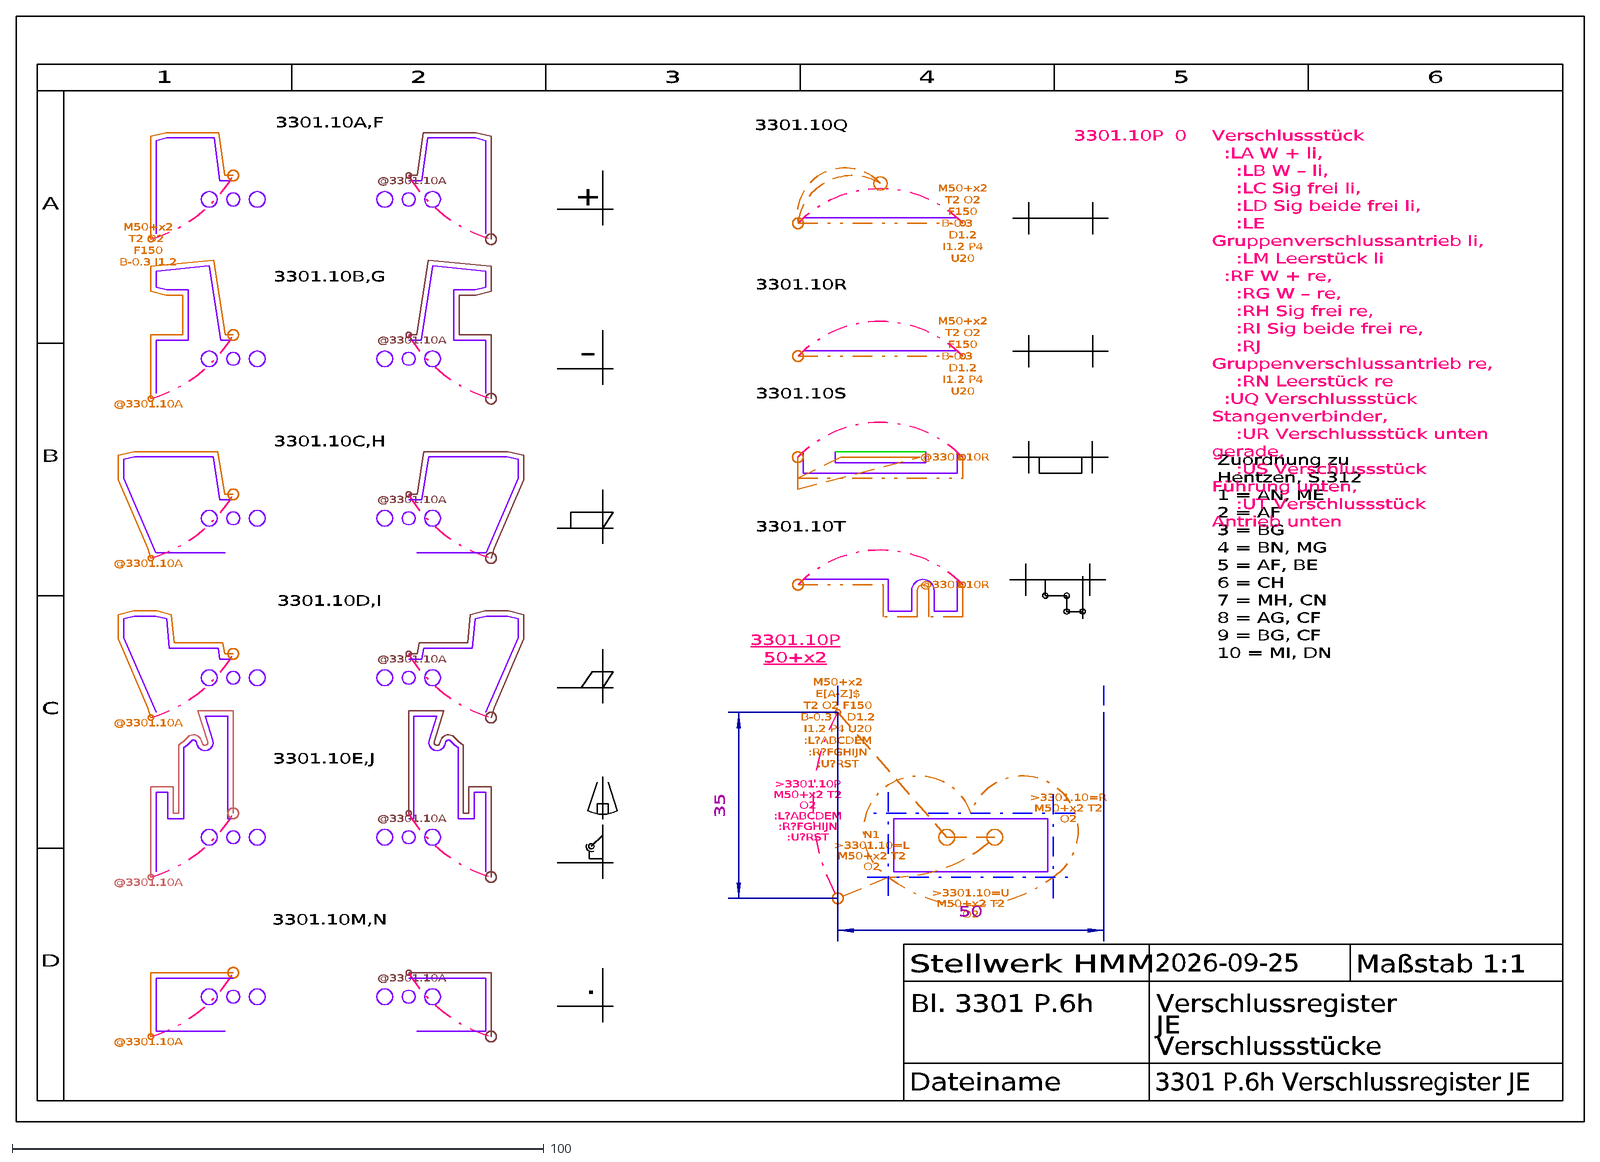
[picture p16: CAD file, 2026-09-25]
DXF2GCode/3301 P.6h Verschlussregister JE.dxf
2026-09-25
3301 P.6h Verschlussregister JE
M50+x2 E[A-Z]$ T2 O2 F150 B-0.3 D1.2 I1.2 P4 U20 :L?ABCDEM :R?FGHIJN :U?RST
N1 >3301.10=L M50+x2 T2 O2
>3301.10=R M50+x2 T2 O2
>3301.10=U M50+x2 T2 O2
M50+x2 T2 O2 F150 B-0.3 I1.2
@3301.10A
M50+x2 T2 O2 F150 B-0.3 D1.2 I1.2 P4 U20
@3301.10R
Zuordnung zu Hentzen, S.312 1 = AN, ME 2 = AF 3 = BG 4 = BN, MG 5 = AF, BE 6 = CH 7 = MH, CN 8 = AG, CF 9 = BG, CF 10 = MI, DN
3301.10A,F
3301.10B,G
3301.10C,H
3301.10D,I
3301.10E,J
3301.10M,N
3301.10Q
3301.10S
3301.10T
3301.10P 50+x2
3301.10P
0
Verschlussstück :LA W + li, :LB W – li, :LC Sig frei li, :LD Sig beide frei li, :LE Gruppenverschlussantrieb li, :LM Leerstück li :RF W + re, :RG W – re, :RH Si
>3301.10P M50+x2 T2 O2 :L?ABCDEM :R?FGHIJN :U?RST
+
–
·
35
50
3301.10R
1
2
3
4
5
6
A
B
C
D
Stellwerk HMM
Verschlussregister JE Verschlussstücke
Dateiname
Bl. 3301 P.6h
Maßstab 1:1

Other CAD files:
DXF2GCode/3816 S.4LPh Tegernsee.dxf
DXF2GCode/3816 S.4RPh Tegernsee.dxf
Projekte2025/2201 Pv Doppelhebelbock m. Schlü.dxf
DXF2GCode/3816 S.3Ph Tegernsee.dxf
DXF2GCode/3816 S.3Th Tegernsee.dxf
DXF2GCode/2010 Ph Schlitze 3mm.dxf
DXF2GCode/2018 Sh 3mm-Schlitz.dxf
DXF2GCode/2019 Ph 3mm-Schlitz.dxf
DXF2GCode/2019 Sv 3mm-Schlitz.dxf
DXF2GCode/2019 Vv 3mm-Schlitz.dxf
DXF2GCode/2052-2053 P.1v Schloss, Schlüssel.dxf
DXF2GCode/2052-2053 P.2v Schloss, Schlüssel.dxf
DXF2GCode/2052-2053 P.3v Schloss, Schlüssel.dxf
DXF2GCode/2055 Ph Doppelschloss.dxf
DXF2GCode/2058 S.2aLh 5 Schlösser.dxf
DXF2GCode/2058 S.2bRh 5 Schlösser.dxf
DXF2GCode/2058 S.4aLh 1 Schloss.dxf
DXF2GCode/2058 S.4bRh 1 Schloss.dxf
DXF2GCode/2059 P.1Lh 5 Schlösser.dxf
DXF2GCode/2059 P.2Rh 5 Schlösser.dxf
DXF2GCode/2059 S.2Rv 5 Schlösser.dxf
DXF2GCode/2059 V.2Rv 5 Schlösser.dxf
DXF2GCode/2059 V.2aLv 5 Schlösser.dxf
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

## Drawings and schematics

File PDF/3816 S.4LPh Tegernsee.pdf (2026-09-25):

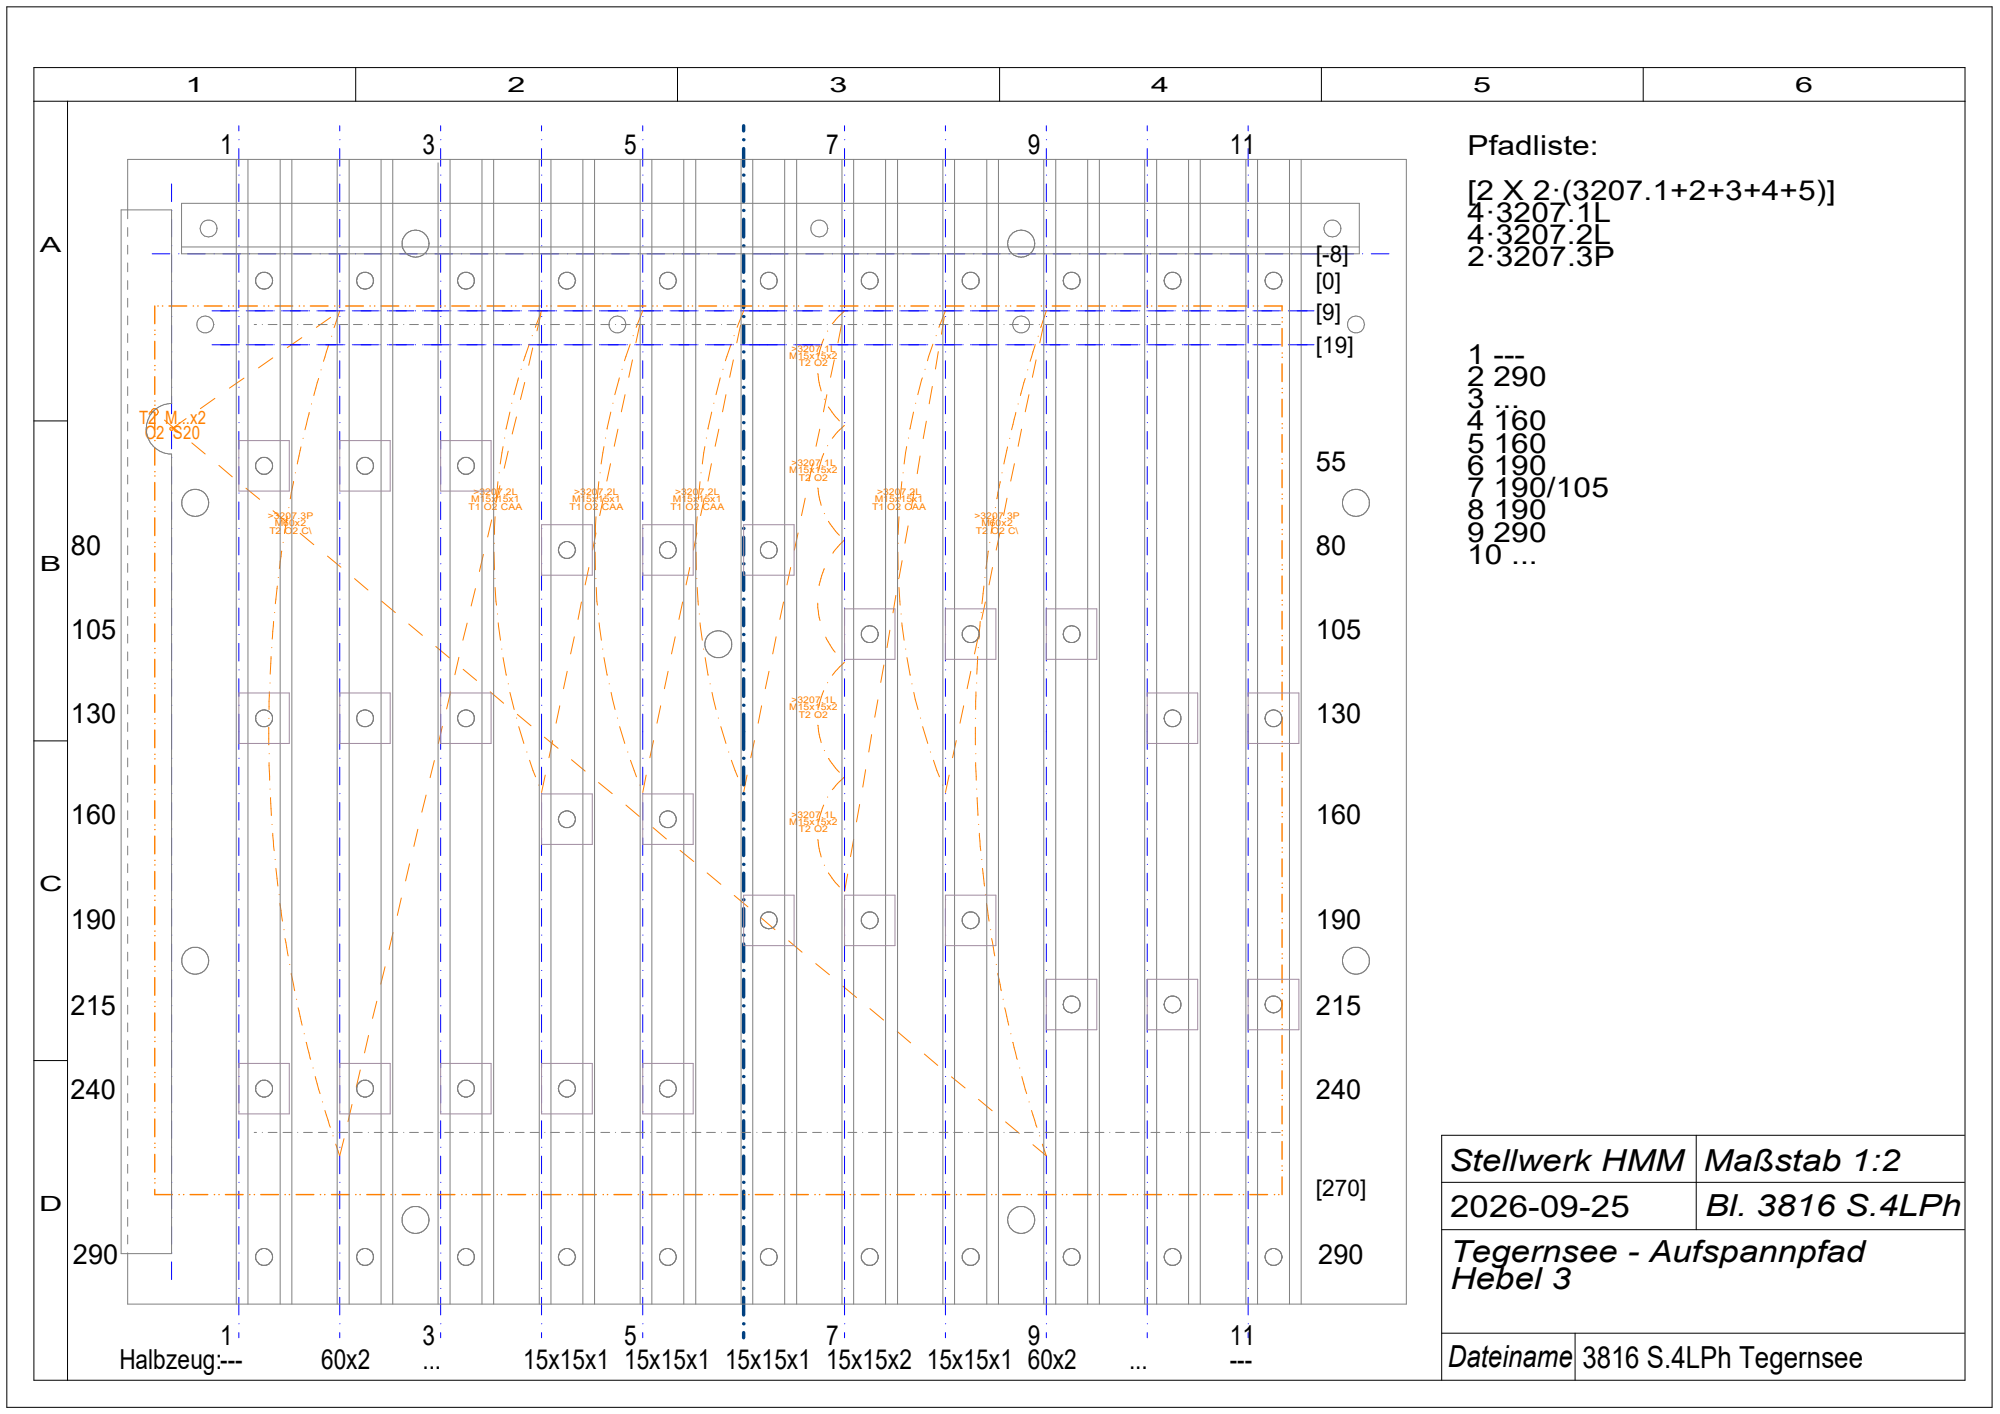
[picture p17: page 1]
---Halbzeug:; Dateiname; Pfadliste:; >3207.2L M15x15x1 T1 O2 CAA; 3816 S.4LPh Tegernsee

Stellwerk HMM | Maßstab 1:2
2026-09-25 | Bl. 3816 S.4LPh

Tegernsee - Aufspannpfad Hebel 3

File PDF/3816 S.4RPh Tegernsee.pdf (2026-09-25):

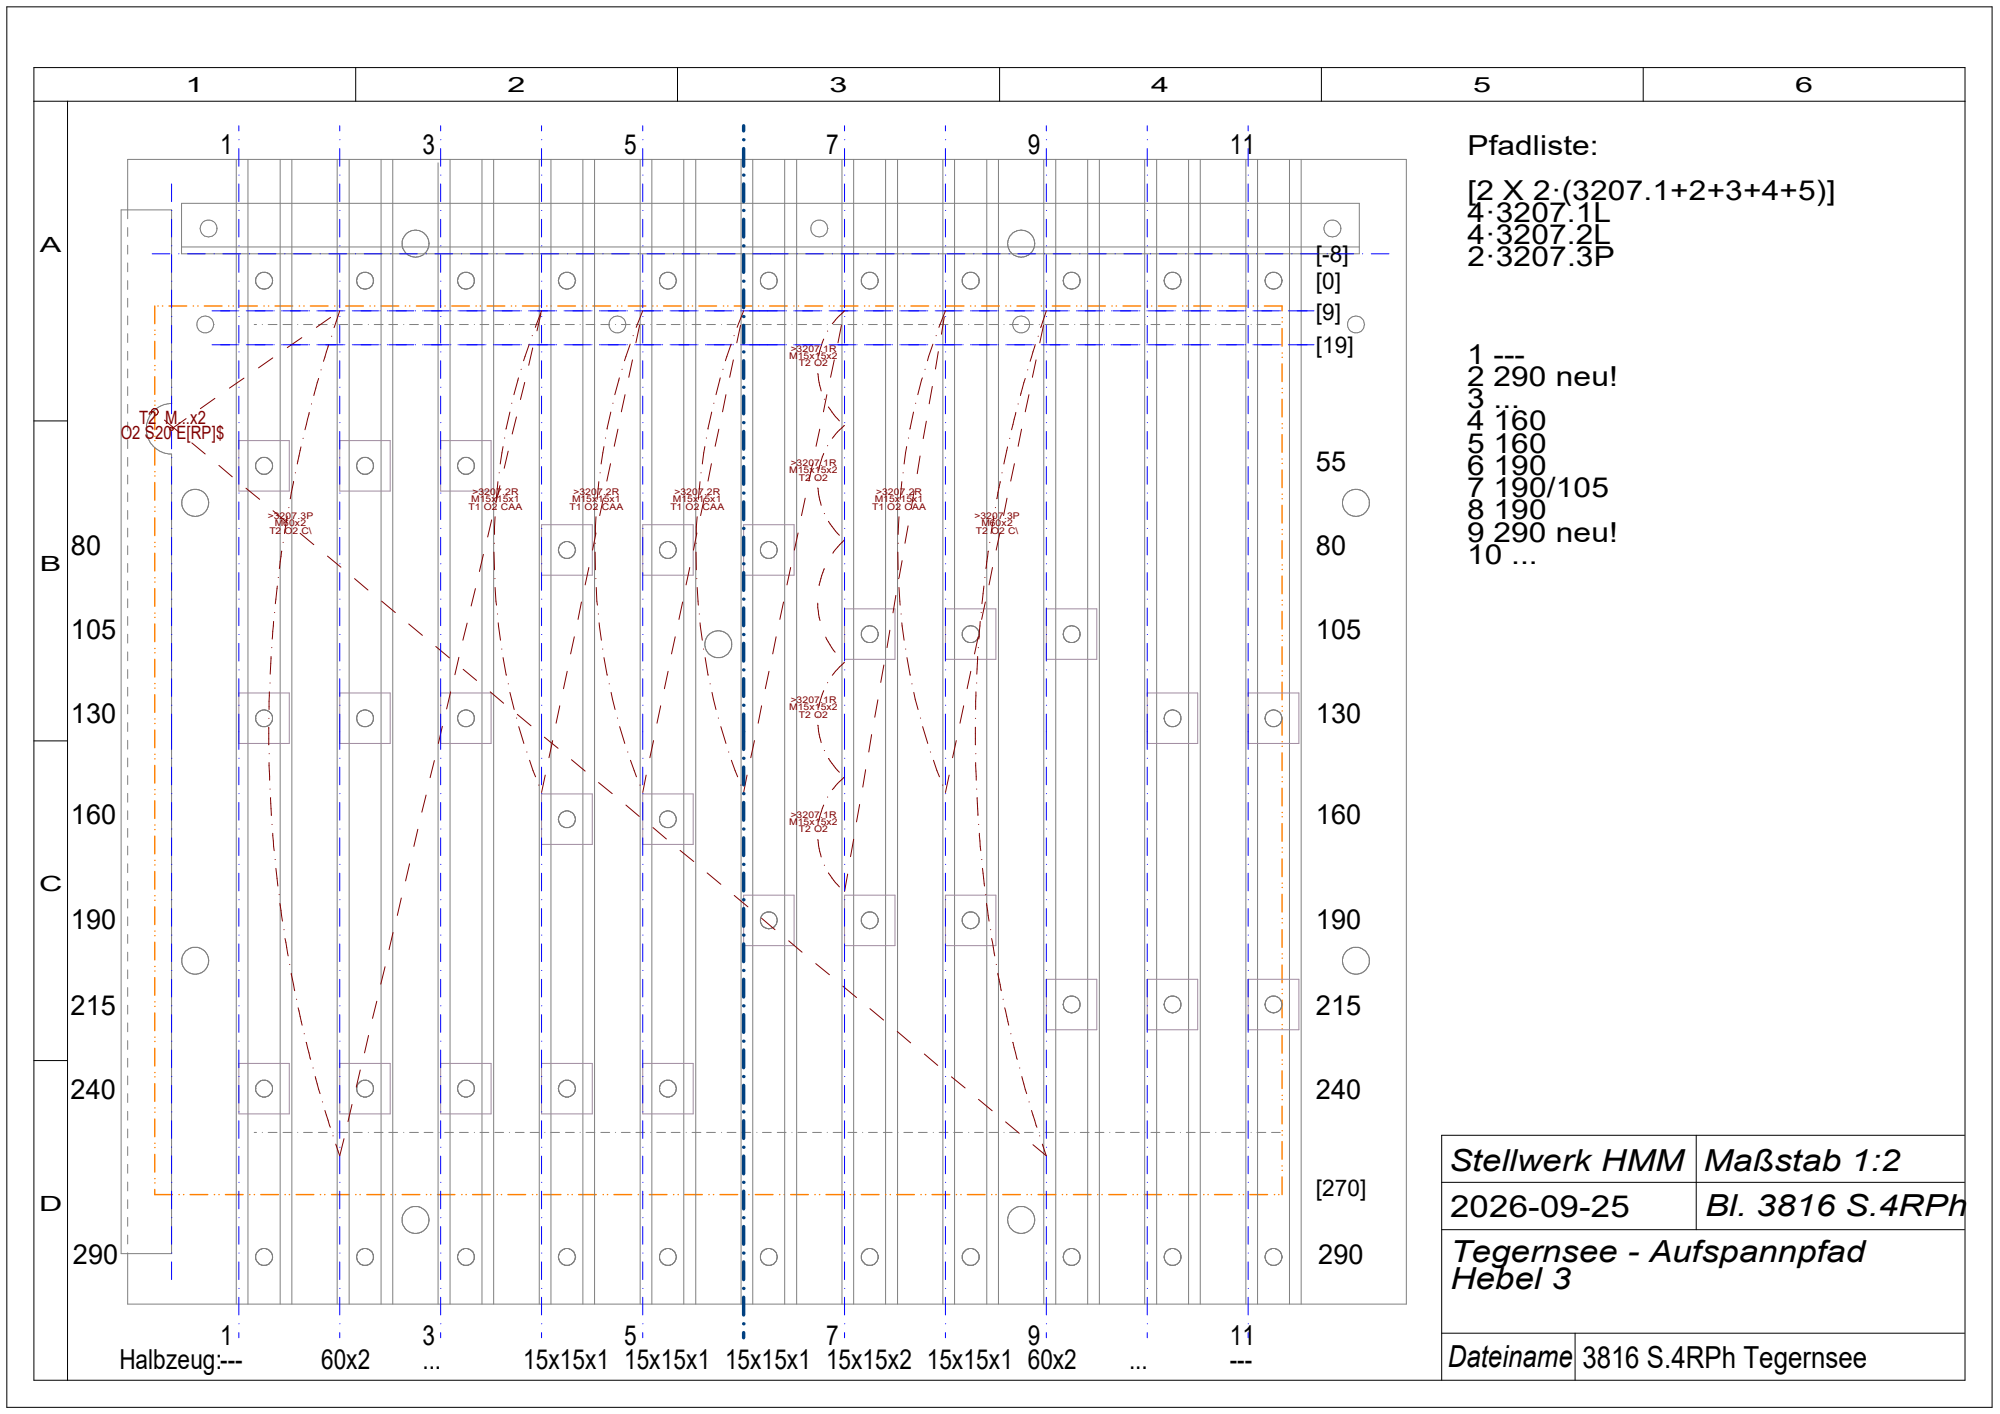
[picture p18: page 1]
Dateiname; 1 --- 2 290 neu! 3 ... 4 160 5 160 6 190 7 190/105 8 190 9 290 neu! 10 ...; ---Halbzeug:; Pfadliste:; O2 CAA; 3816 S.4RPh Tegernsee

Stellwerk HMM | Maßstab 1:2
2026-09-25 | Bl. 3816 S.4RPh

Tegernsee - Aufspannpfad Hebel 3

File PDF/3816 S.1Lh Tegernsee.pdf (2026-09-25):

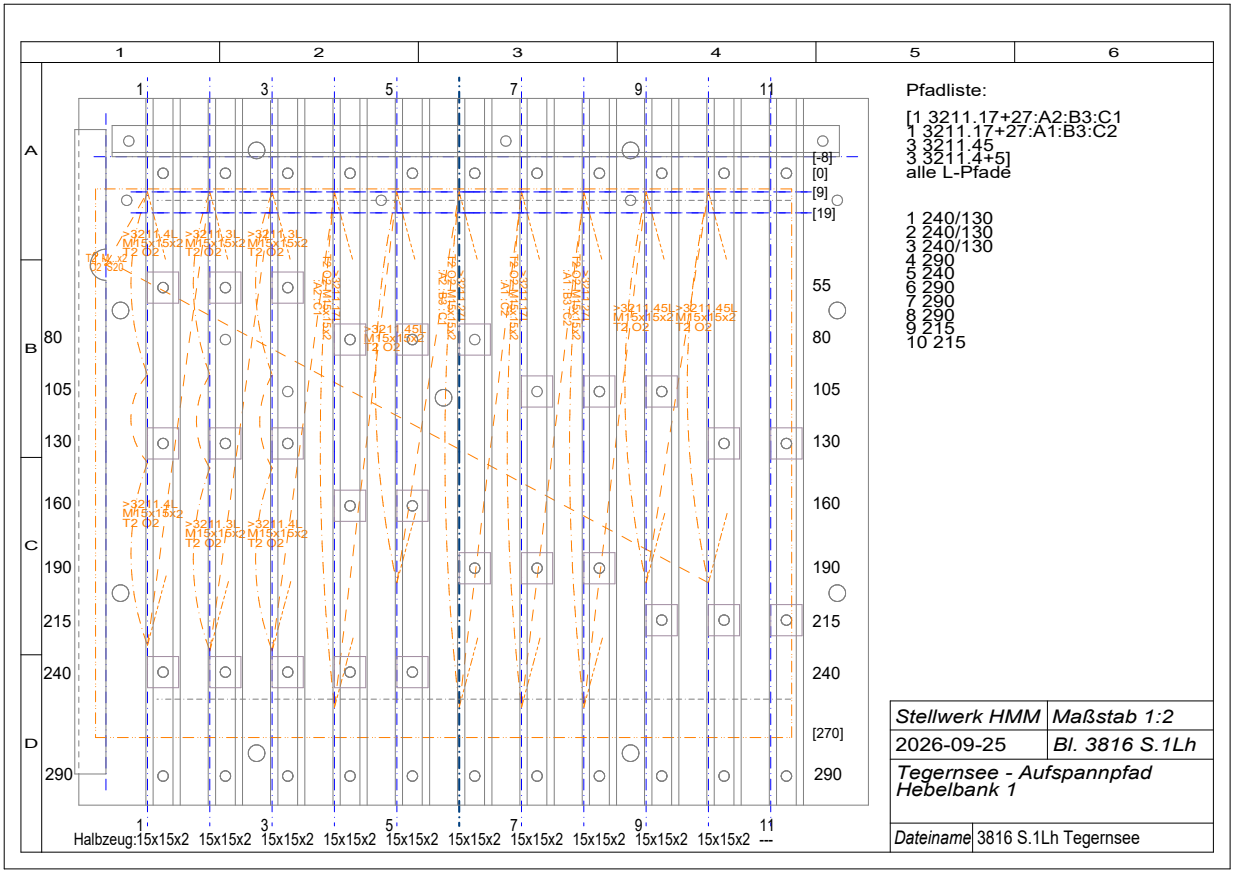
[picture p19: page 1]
15x15x2 15x15x2 15x15x2 15x15x2 15x15x2 15x15x2 15x15x2 15x15x2 15x15x2 15x15x2 ---Halbzeug:; Dateiname; Pfadliste:; 3 3211.45 3 3211.4+5] alle L-Pfade; 3816 S.1Lh Tegernsee

Stellwerk HMM | Maßstab 1:2
2026-09-25 | Bl. 3816 S.1Lh

Tegernsee - Aufspannpfad Hebelbank 1

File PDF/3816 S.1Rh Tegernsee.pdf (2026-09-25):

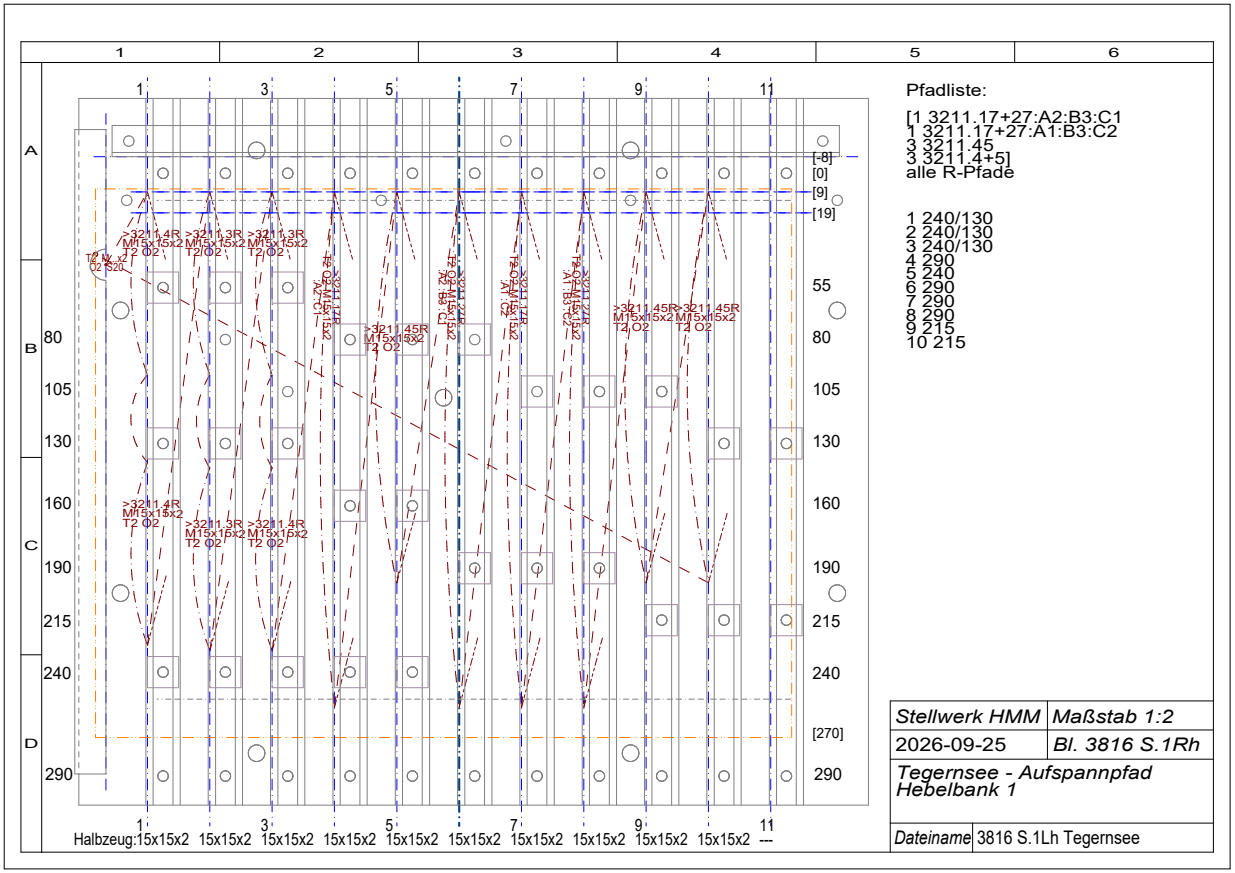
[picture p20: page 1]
15x15x2 15x15x2 15x15x2 15x15x2 15x15x2 15x15x2 15x15x2 15x15x2 15x15x2 15x15x2 ---Halbzeug:; Dateiname; Pfadliste:; 3 3211.45 3 3211.4+5] alle R-Pfade; 3816 S.1Lh Tegernsee

Stellwerk HMM | Maßstab 1:2
2026-09-25 | Bl. 3816 S.1Rh

Tegernsee - Aufspannpfad Hebelbank 1

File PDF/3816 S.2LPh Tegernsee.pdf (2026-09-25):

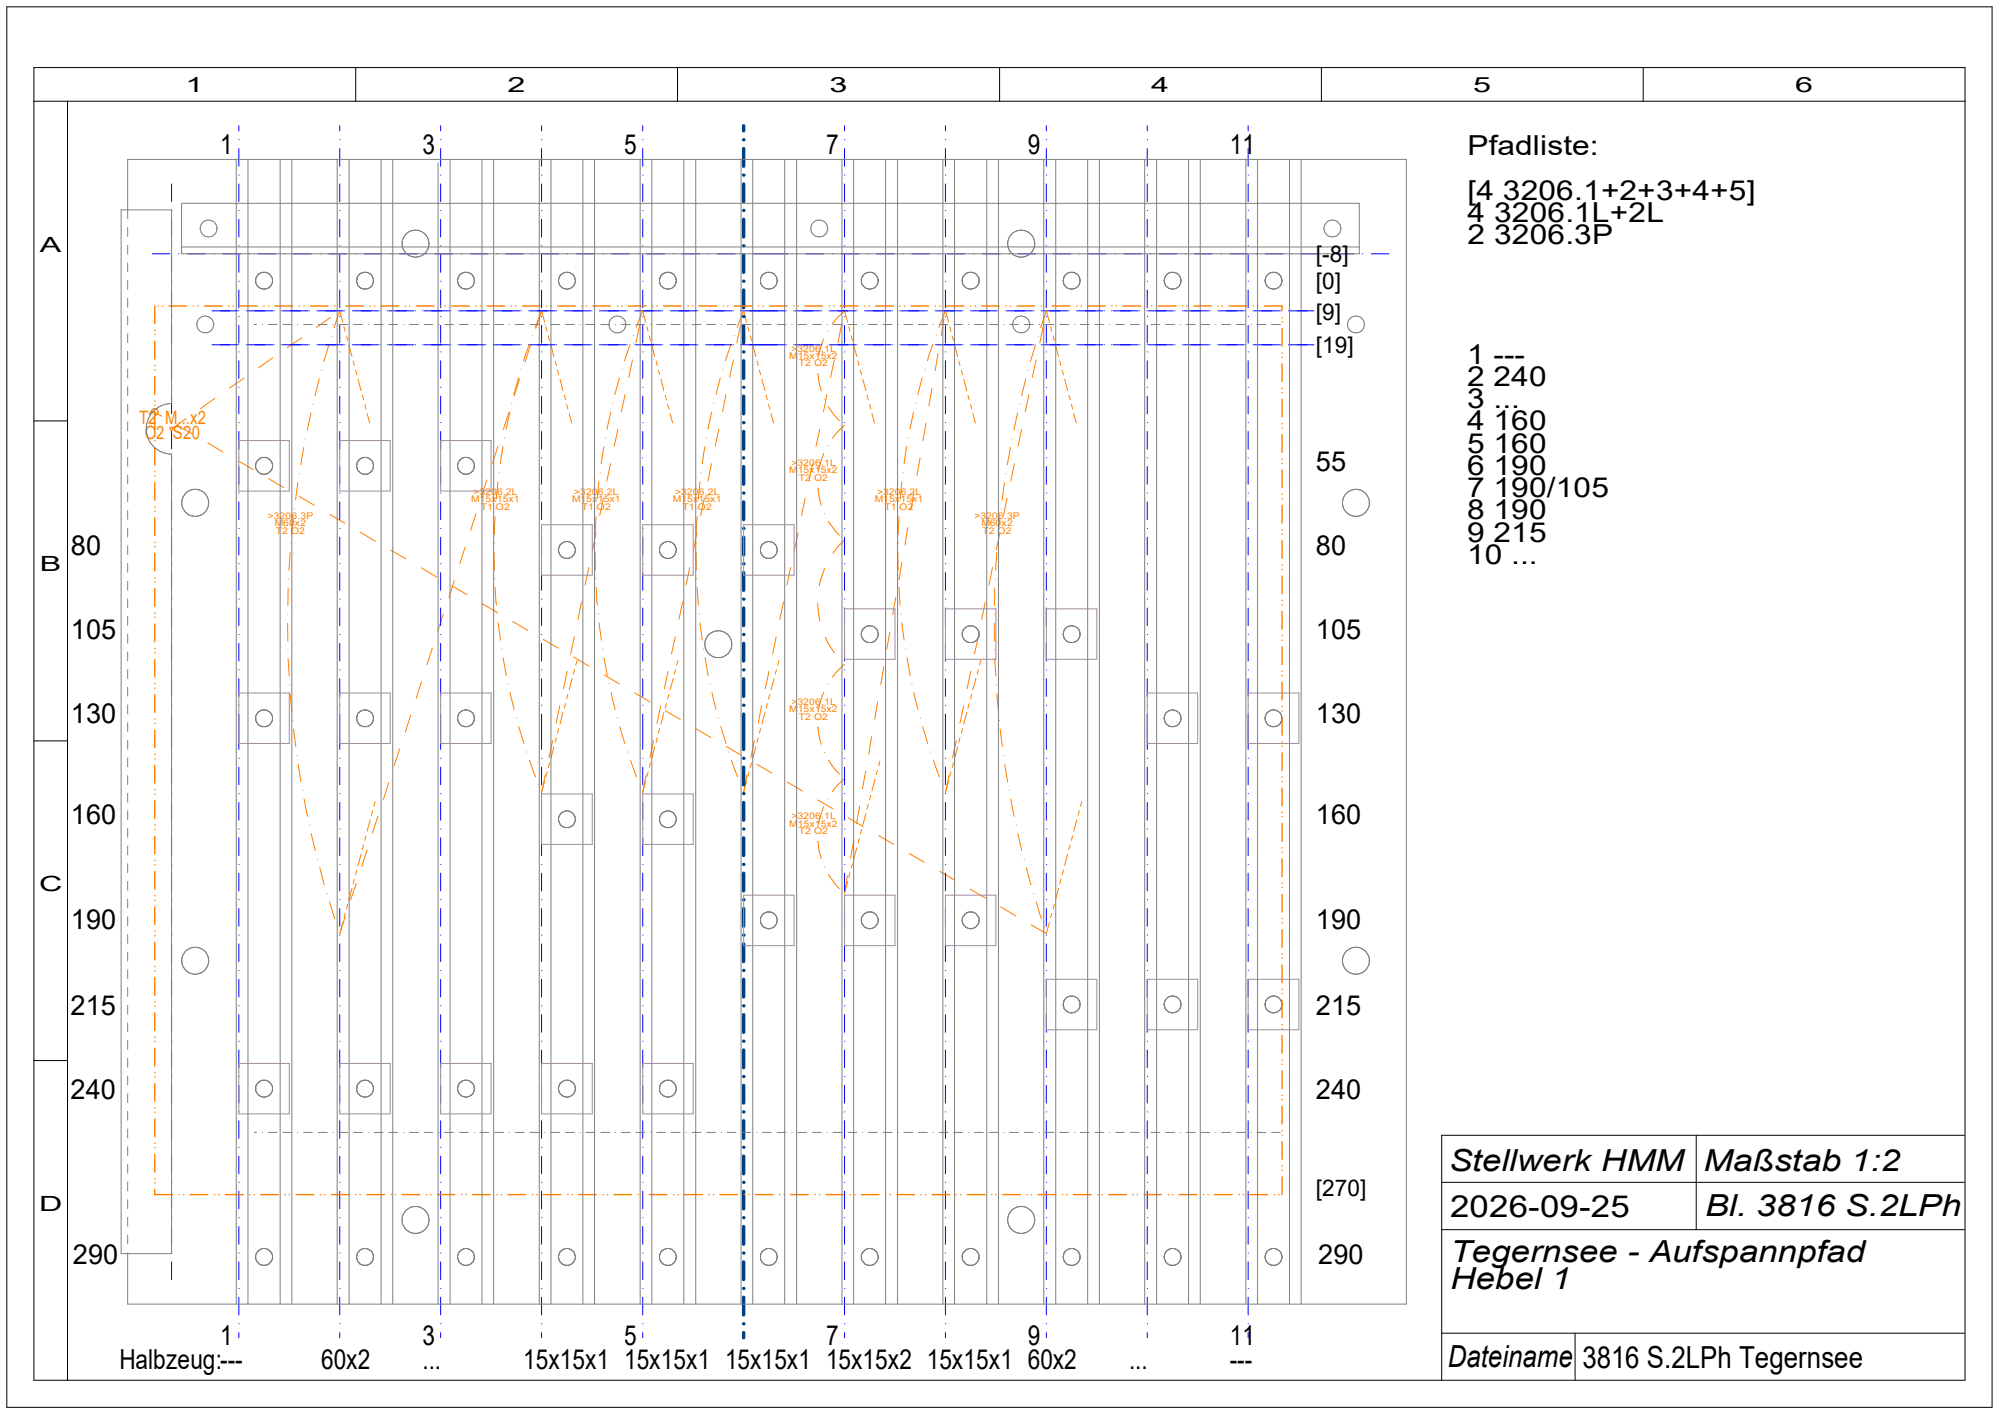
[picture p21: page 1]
---Halbzeug:; Dateiname; Pfadliste:; 3816 S.2LPh Tegernsee

Stellwerk HMM | Maßstab 1:2
2026-09-25 | Bl. 3816 S.2LPh

Tegernsee - Aufspannpfad Hebel 1

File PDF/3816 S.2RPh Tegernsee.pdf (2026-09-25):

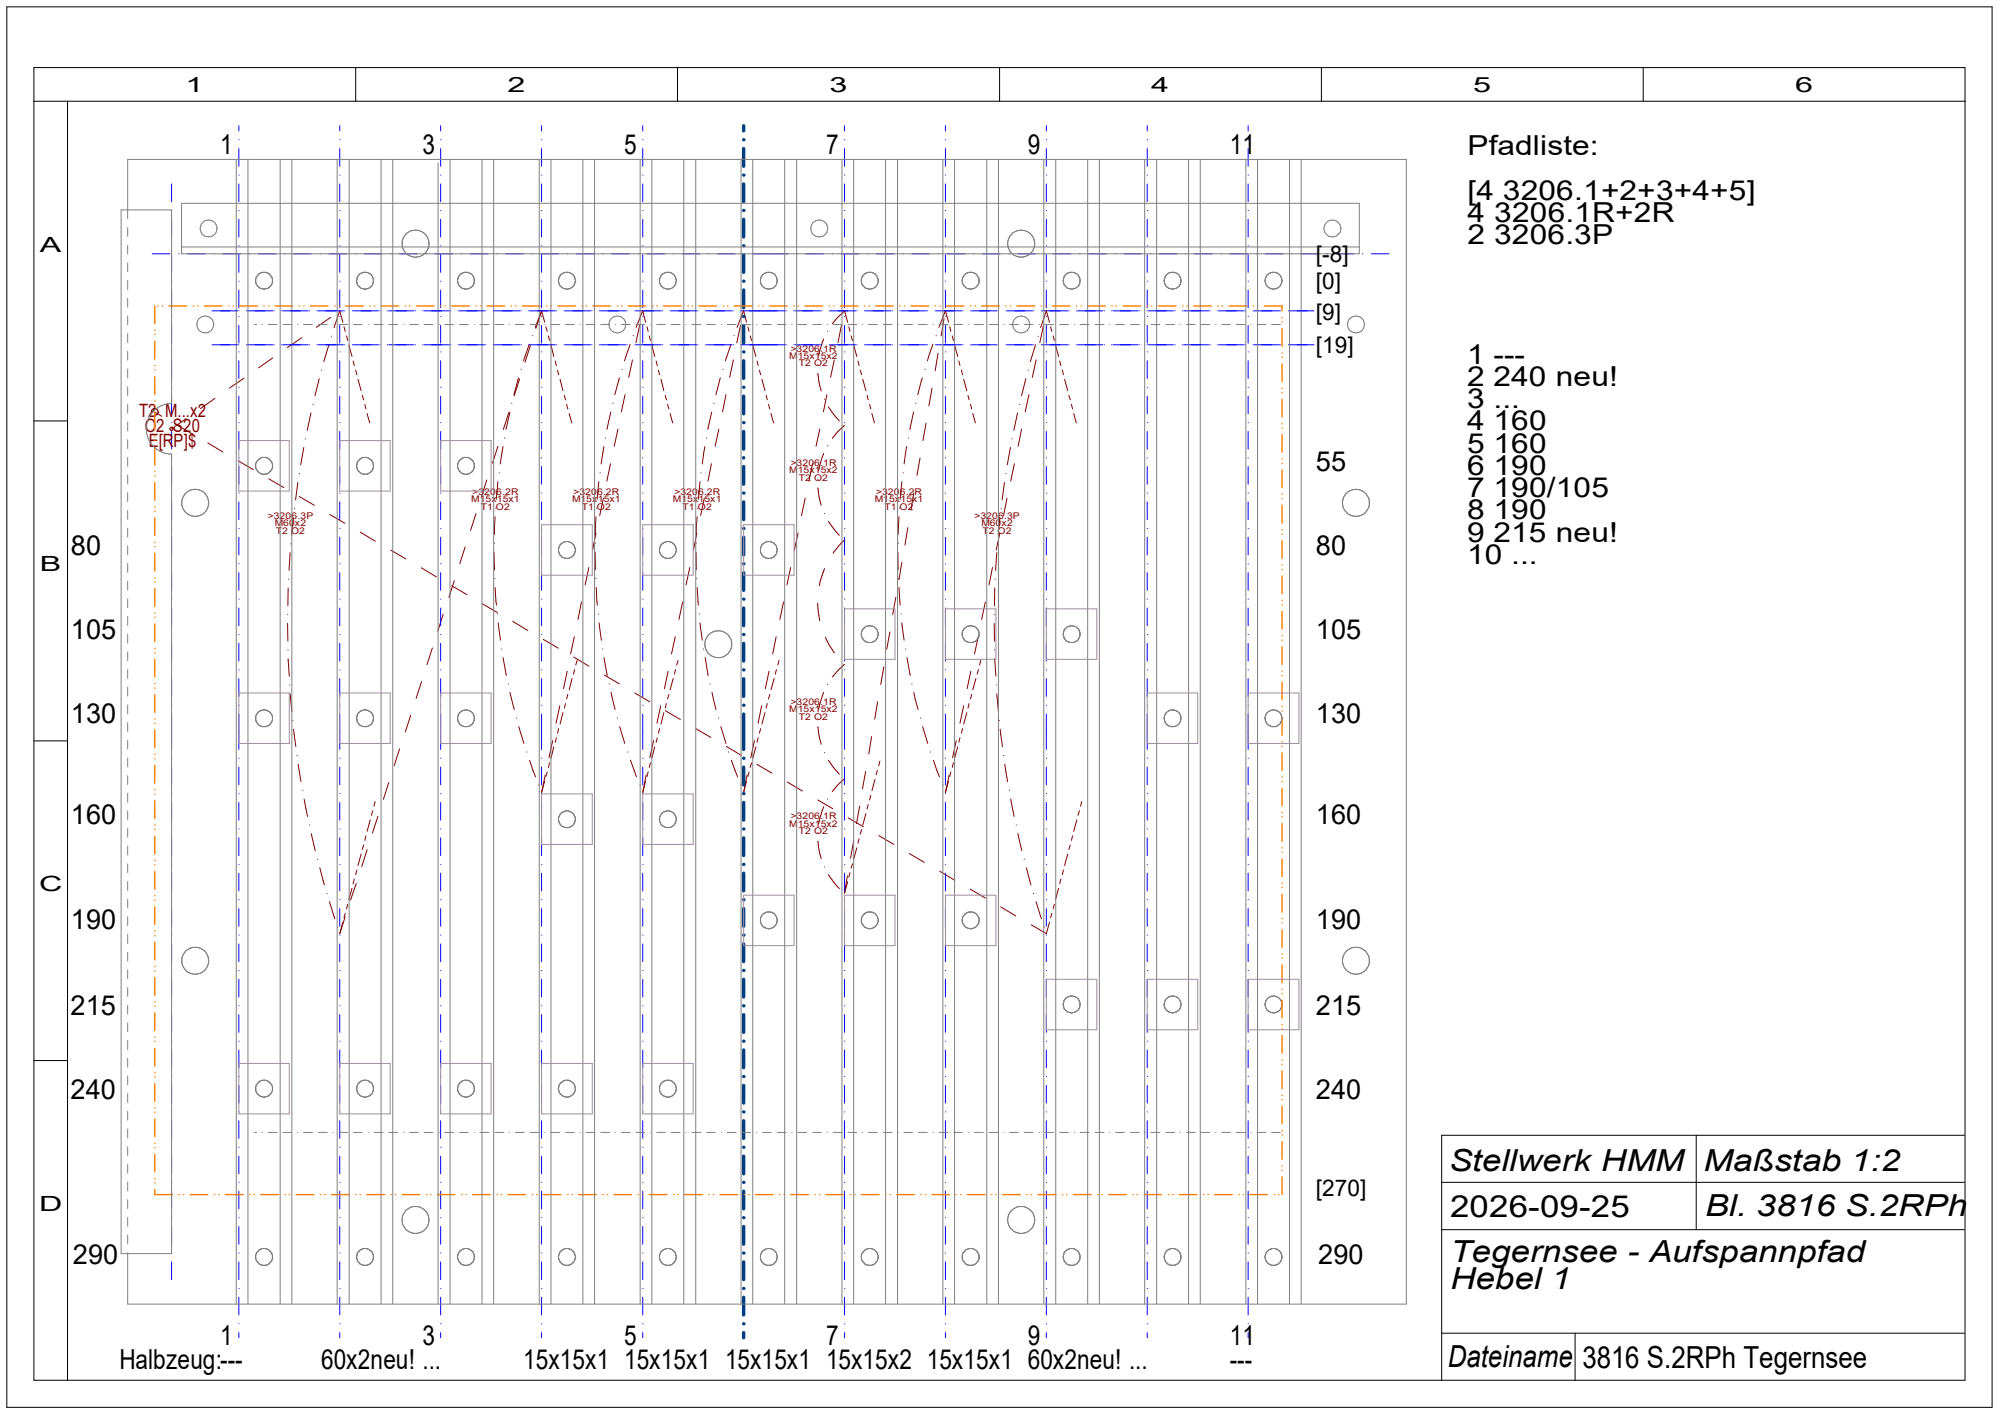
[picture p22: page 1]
60x2neu! ...; 15x15x1 15x15x1 15x15x1 15x15x2 15x15x1 60x2neu! ...; ---Halbzeug:; Dateiname; Pfadliste:; 1 --- 2 240 neu! 3 ... 4 160 5 160 6 190 7 190/105 8 190 9 215 neu! 10 ...; 3816 S.2RPh Tegernsee

Stellwerk HMM | Maßstab 1:2
2026-09-25 | Bl. 3816 S.2RPh

Tegernsee - Aufspannpfad Hebel 1

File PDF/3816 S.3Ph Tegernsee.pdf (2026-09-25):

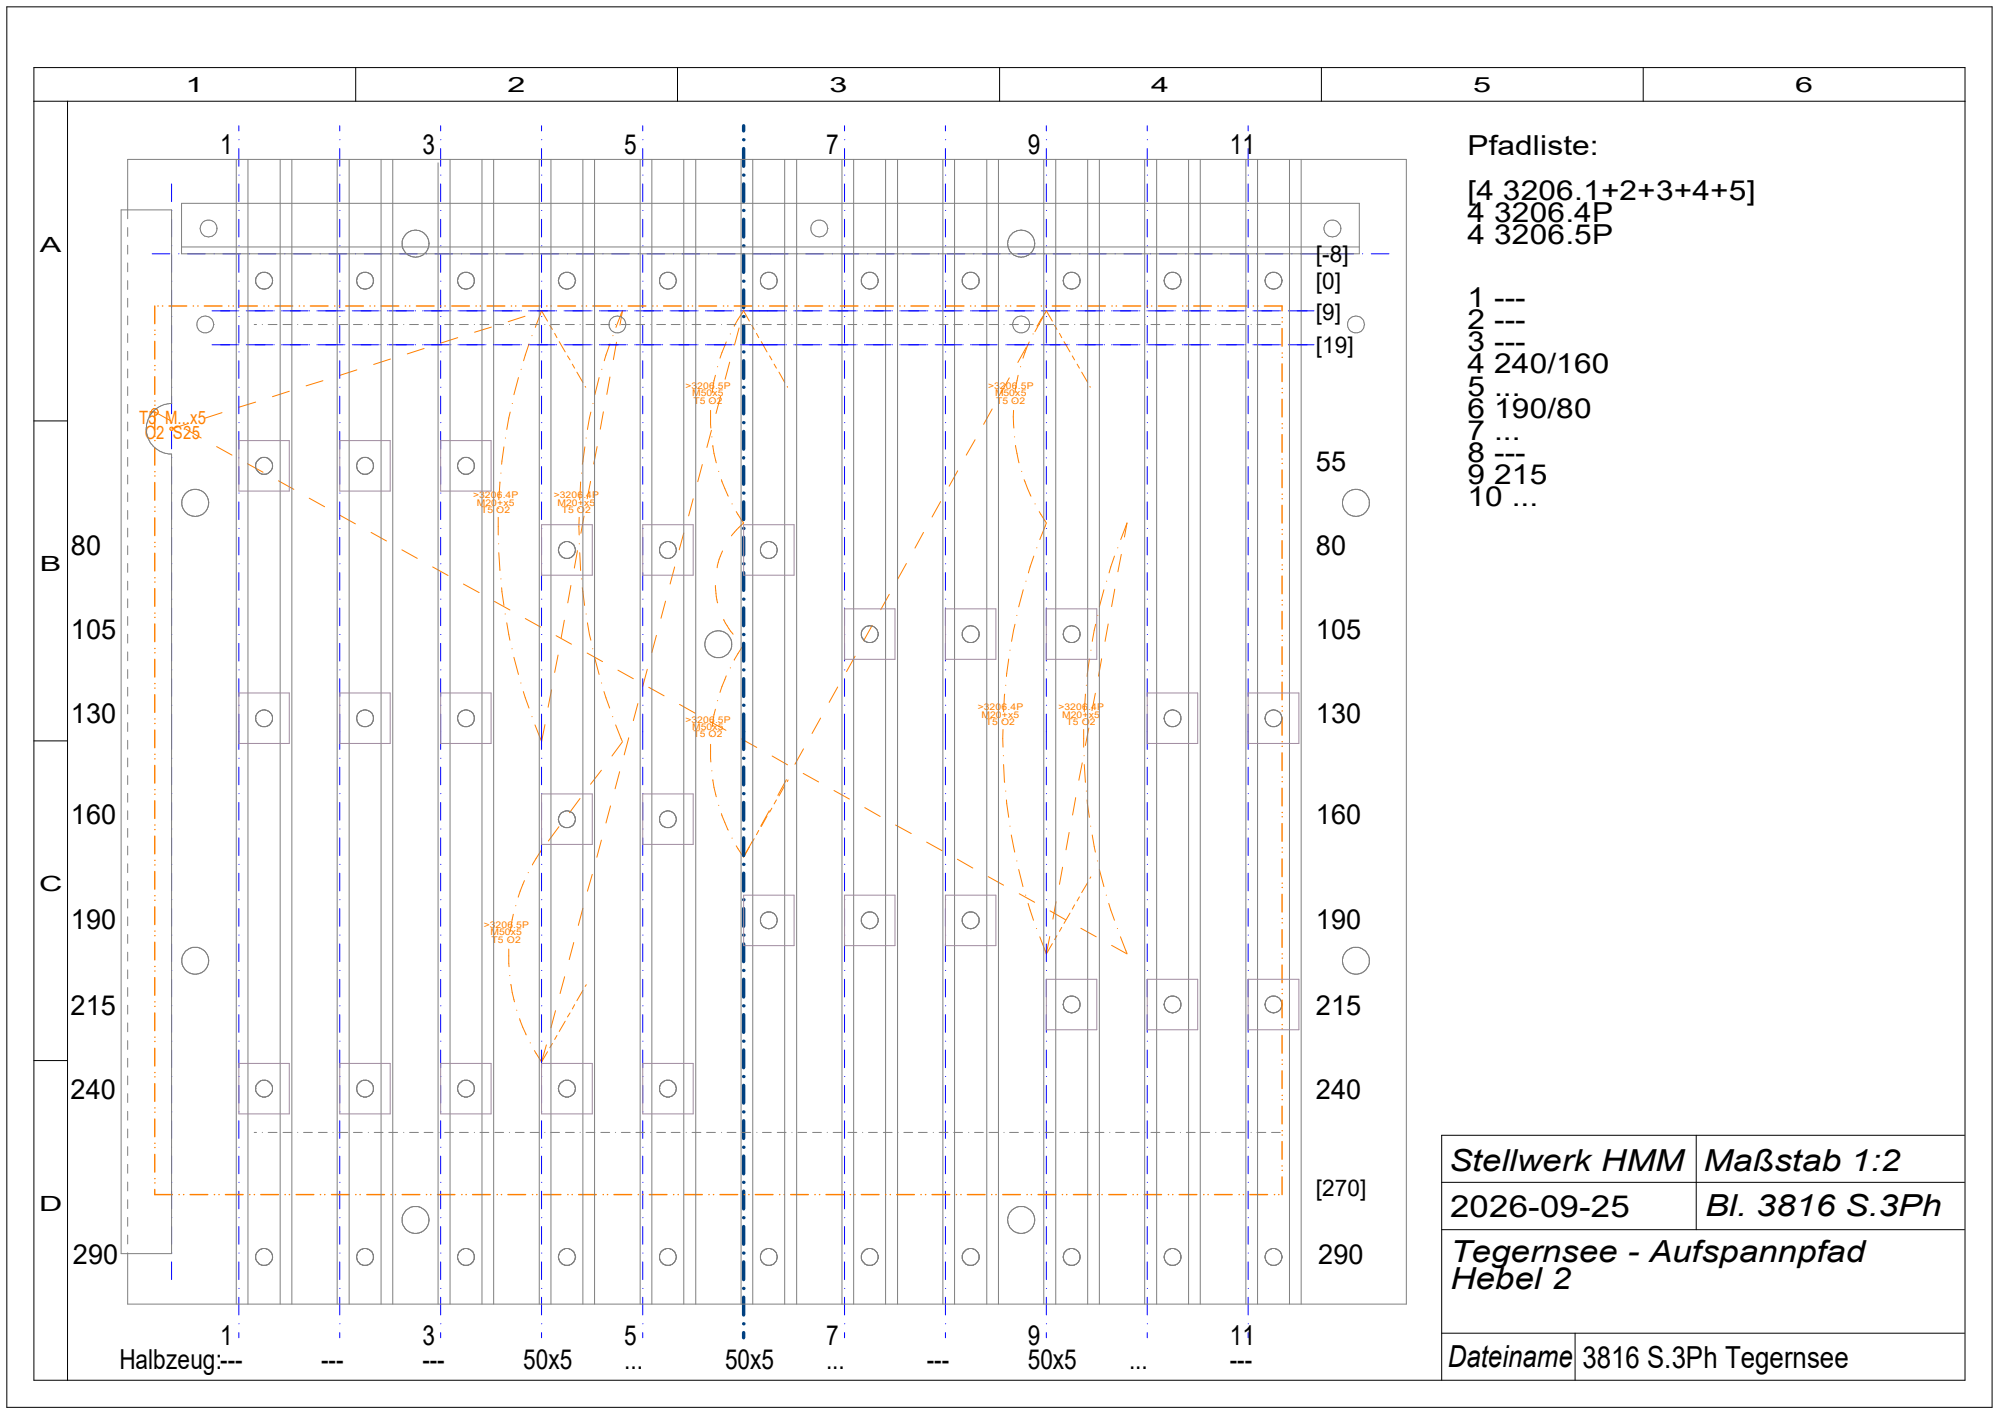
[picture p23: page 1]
---Halbzeug:; Dateiname; Pfadliste:; 3816 S.3Ph Tegernsee

Stellwerk HMM | Maßstab 1:2
2026-09-25 | Bl. 3816 S.3Ph

Tegernsee - Aufspannpfad Hebel 2

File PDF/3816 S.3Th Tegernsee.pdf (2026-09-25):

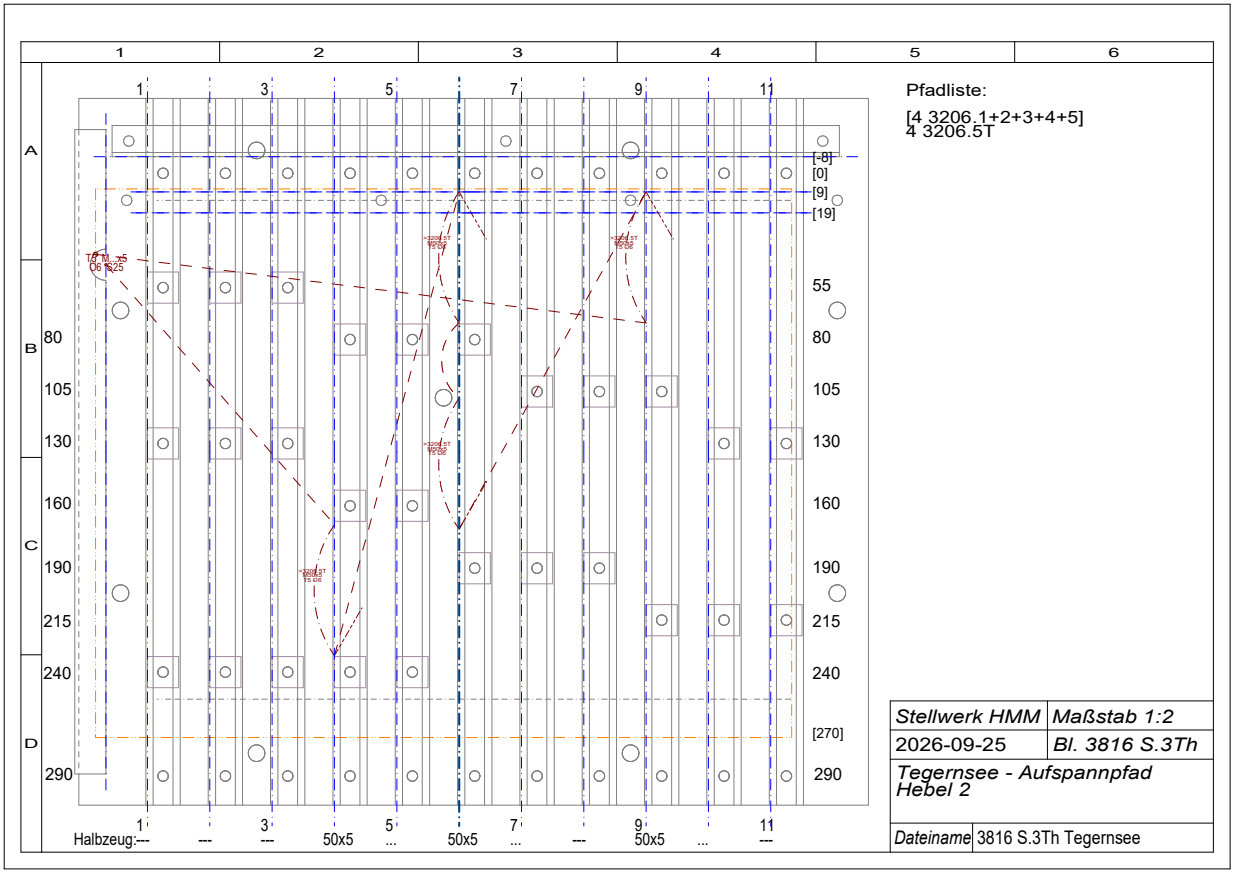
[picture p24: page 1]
Dateiname; ---Halbzeug:; Pfadliste:; 3816 S.3Th Tegernsee

Stellwerk HMM | Maßstab 1:2
2026-09-25 | Bl. 3816 S.3Th

Tegernsee - Aufspannpfad Hebel 2

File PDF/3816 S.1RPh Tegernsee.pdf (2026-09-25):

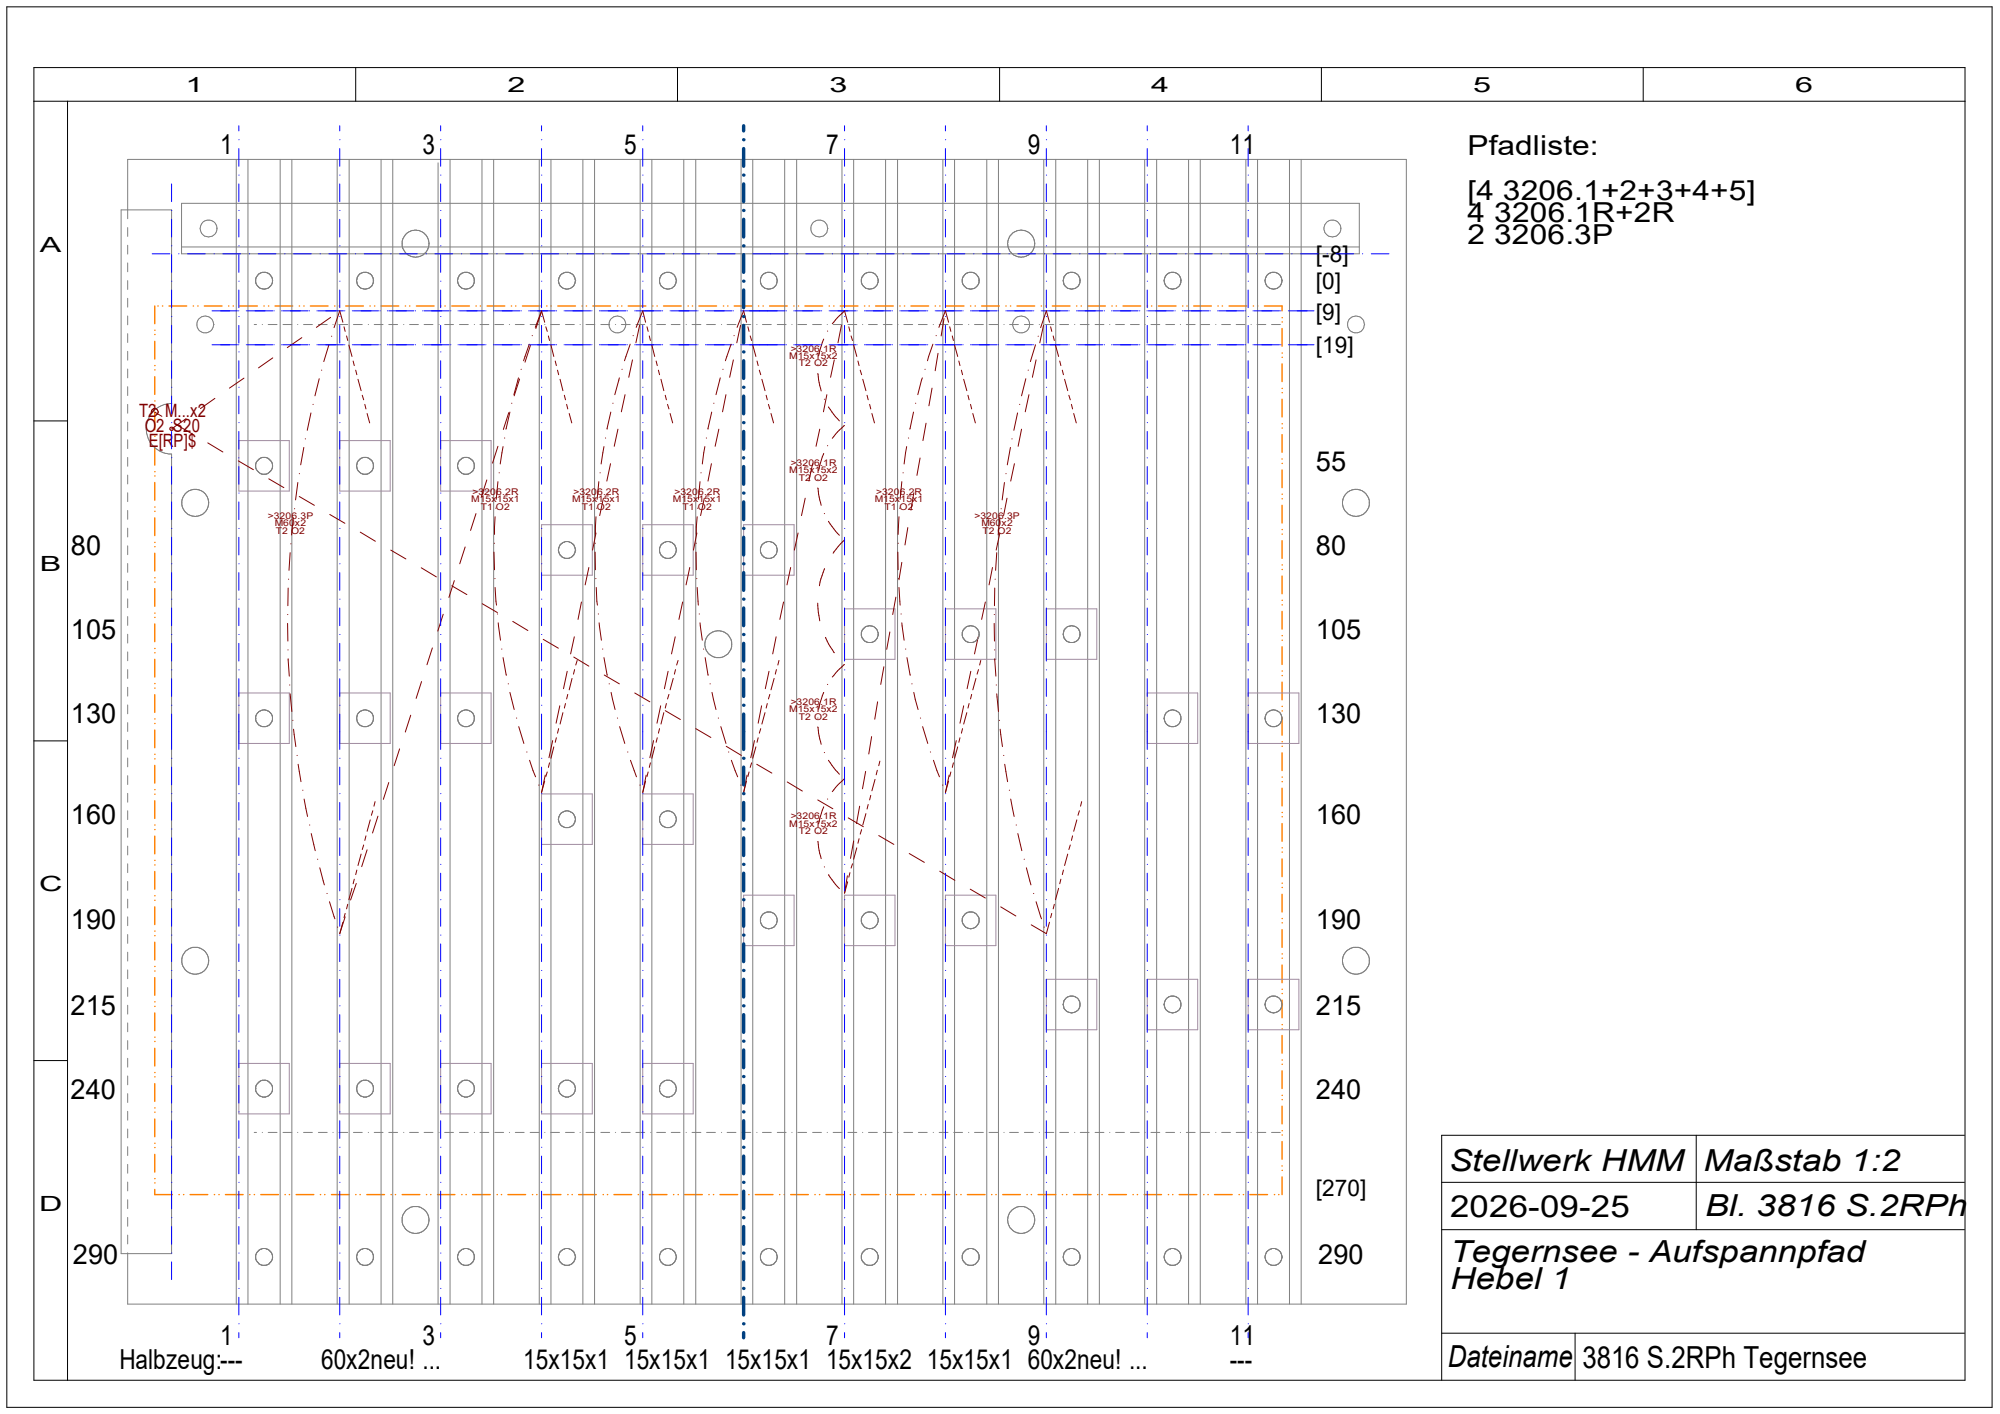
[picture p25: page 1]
Pfadliste:; Halbzeug:; ---...60x2neu!15x15x115x15x215x15x1 15x15x1 15x15x1...60x2neu!---; 3816 S.2RPh Tegernsee; Bl. 3816 S.2RPh; Dateiname

Stellwerk HMM Maßstab 1:2
Tegernsee - Aufspannpfad Hebel 1

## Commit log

2025-03-24 Added measuring collect for router bits; updated 2052-2053 (key+lock); added 8004 (2 locks)
    [2052-2053 P.1v.dxf, 2916 Ph.dxf, 8004 P.1Lh.dxf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]
2025-03-26 Added measuring collet for router bits; updated 2052-2053 (key+lock); added 8004 (2 locks)
    [2052-2053 P.1v.dxf, 2916 Ph.dxf, 8004 P.1Lh.dxf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]
2025-03-31 Added project 8005; corrected 8004 (some M's changed)
    [2052-2053 P.1v.dxf, 8004 P.1Lh.dxf, 8005 Ph.dxf]
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2025-10-05 2653 Weichenstellung: Zwei "Zungenschieber"
    Änderungen
    - Ein Weichenschloss soll zwei Schieber (einen
    je Zunge) haben. Um das so darzustellen, gibt
    es nun 2653.2 und 2653.3, mit jeweils einem
    kleinen ("für die anliegende") und einem
    großen (für die "abliegende") Ausschnitt.
    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
    [2655 Ph W-, Gsp-, Signal-Antrieb.dxf, 2913 P.1Oh Aufspannplatte oben hi.dxf, 2913 P.2Ph Aufspannplatte oben vo.dxf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]
2025-10-11 Zusammenbauten überarbeitet, alte Dateien gelöscht
    - Zusammenbau für Zentralschloss 5701 dokumentiert
    - Zusammenbau für Weichenantriebe 2655 dokumentiert
    - Lehre 2655.99 für Weichenantrieb 2655 ergänzt
    Korrekturen
    - alte Dateien ohne Titel aus Projekte2025 entfernt
    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
    [2010 Ph.dxf, 2050-2051 P.1v.dxf, 2050-2051 P.2v.dxf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]
2025-10-26 2201: Seilführung vorbildgerecher, Rasteneinfall korrigiert
    - Die Seilführung ist nicht mehr parallel nach unten,
    sondern zusammenlaufend.
    - Die Rastanausnehmungen hatten schräge (radiale) Seiten,
    sodass durch Ruckeln am Hebel (oder auch durch den
    Signalarm!) die Raste herausspringen konnte (was sie
    sinnlos macht).
    Die Seiten der Rastenausnehmungen sind nun parallel zum
    Radius durch die Ausnehmungsmitte und damit "selbst-
    sichernd".
    ---
    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
    [2201 Pv Doppelhebelbock m. Schl.dxf]
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2025-10-27 205*: Überarbeitung Bartschloss
    - Die Konstruktion des Bartschlosses hatte mehrere Fehler:
    (a) der Schlüsselbart stand zu weit vor und kollidierte mit dem Riegel;
    (b) das Schlüsselrohr war nicht bis ganz unten durchgezogen, sodass der
    Schlüssel nicht gut geführ wurde;
    Diese Probleme sind nun hoffentlich korrigiert:
    (-) Der Bart hat nun ein 1,5mm-Raster (statt vorher 2mm) und wurde
    dadurch kürzer = kollidiert nicht mehr mit Riegel.
    (-) Die d-Zacke liegt aber um 2,5 mm weiter außen, damit der Schlüssel
    bei c=0 nicht zu dünn wird (dort muss die ganze Kraft zum/vom Riegel
    durch! - also inbesondere bei einem festgelegten Schloss die Kraft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
2025-11-02 570*, 580*: Demoprojekt in Standardordner verschoben
    - "Waldhof" au "Kreuzdorf" umbenannt, in Ordner CAD und Projekte2025 verschoben.
    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
    [2655 Ph W-, Gsp-, Signal-Antrieb.dxf, 5708 S.11Ph Zschl Kreuzdorf Alu.dxf, 5708 S.12Ph Zschl Kreuzdorf Acryl 1.dxf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]
2025-11-03 220*: Hebelbock - Schildchen auf Hebel ergänzt
    - 2201: Schildchen 2201.16/1 für Beschriftung auf Hebel ergänzt.
    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
    [2201 Pv Doppelhebelbock m. Schl.dxf]
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2025-11-12 2052, 2053: bartschloss überarbeitet
    - Bartteilung 1,5mm, weil vorher Bart an Riegel angestoßen ist
    - Schlüsselrohr geht bis ganz nach unten für bessere Führung des Schlüssels beim Einstecken
    - neue Pfadkonstruktion mit weniger Copy-Paste
    - Umbenennung aller Bartschloss-Dateien auf 2052-2053*
    - alte 2201-Datei entfernt
    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
    [2052 P.1v Schloss, Schlüssel A-E.dxf, 2052-2053 P.1v Schloss, Schlüssel.dxf, 2052-2053 P.2v Schloss, Schlüssel.dxf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]
2025-11-12 Alte Dateien gelöscht
    - 2058S-Dateien gelöscht
    - .gitignore um Commit*.txt erweitert
    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
    [2058 S.1Lh 5 Schlösser.dxf, 2058 S.2Rh 5 Schlösser.dxf, 2058 S.3Lh 5 Schlösser.dxf]
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2025-11-17 265*: Weichen- und Signalantrieb
    - Signalplatte ergänzt (Träger für Signalantrieb und Formsignal)
    - nur mehr eine Pfadzeichnung
    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
    [2655 P.1h W-, Gsp-, Signal-Antrieb.dxf]
2025-11-17 220*: Signalhebelbock
    - Schildchengröße an Hebelschildchen angepasst
    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
    [2201 Pv Doppelhebelbock m. Schl.dxf]
2025-11-19 320*: Deutsche Hebel
    - Einzelhebel DE (Konstruktion und Pfade) neu
    - Doppelhebel DE (nur Konstruktion) neu
    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
    [3201 Pv Einzelhebel DE.dxf]
2025-11-27 3202: Deutscher Doppelhebel
    - Doppelhebel DE Pfade neu
    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
    [3202 Pv Doppelhebel DE.dxf]
2025-12-11 220: Pfade neu erzeugt
    - Für Signalhebelbock 220 Pfade nach Ergänzung der
    kleinen Rollen neu erzeugt, alte Dateien entfernt.
    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
    [2201 Pv Doppelhebelbock m. Schl.dxf, 2208 S.01Lh Hebelbock Gr.oben.dxf, 2208 S.02Rh Hebelbock Gr.oben.dxf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]
2025-12-14 220: Korrekturen
    a. Schlösser ca 1mm weiter außen, damit Seil dran vorbeigeht
    b. Weiteres Vefestigungsloch
    c. vorderes Unterzugsröllchen 1mm nach vorne
    d. Rahmenschlitz für Rastenzapfen 0,5mm breiter
    e. Anschlag .51 um 1mm nach vorne
    f. Schildchen schmäler, damit sie nicht an Rastengewicht anschlagen
    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
    [2201 Pv Doppelhebelbock m. Schl.dxf]
2025-12-19 220: Signalhebelbock - Befestigung verschoben
    - Befestigungslöcher verschoben, weil zu nahe an den Röllchenachsen.
    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
    [2201 Pv Doppelhebelbock m. Schl.dxf]
2025-12-19 580: Kreuzdorf - Schlüsselbrett ergänzt
    - österreichisches Schlüsselbrett ergänzt:
    -- Druck
    -- Türrahmen für Gittereinsatz
    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
    [5803 Ph Türe Schlüsselbrett.dxf]
2025-12-25 Directoryaufteilung für PDFs, DXFs und GCode-Dateien geändert
    - Projekte2025 in zwei Subdirs PDF und DXF2GCode zerlegt
    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
    [2010 Ph Schlitze 3mm.dxf, 2018 Sh 3mm-Schlitz.dxf, 2019 Ph 3mm-Schlitz.dxf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]
2026-01-03 265: Weichenantrieb neu konstruiert
    Die bisherigen Weichenantriebe hatten folgende Probleme:
    a) zu viel Reibung (wird sich mit Hebeln, die als Seile Fäden
    verwenden, sicher nicht bewegen lassen)
    b) ungenaue Bewegung (v.a. wegen des Drahtbügels)
    c) nur aus 2 Richtungen mit Gestänge verbindbar
    d) Riegelkonstruktion "planlos"
    Die neue Konstruktion 2654 soll alle diese Nachteile vermeiden.
    - Benennung von Projekten nun einstellig; Reihenfolge von
    Pfaddateien über Buchstaben.
    (Die Änderung ist noch nicht in 1000 nachgetragen)
    - 265: Einige alte Blätter gelöscht
    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
    [2654 Ph W- und Gsp-Antrieb.dxf, 2658 S.12L 6W-, 2S-Antriebe.dxf, 2658 S.13R 6W-, 2S-Antriebe.dxf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]
2026-01-04 265: Weichenantrieb 2654 korrigiert
    Nach dem Bau eines Prototyps 2654 haben sich folgende
    Änderungen ergeben:
    a) Die Führungsplatte entfällt, sie ist nicht nötig.
    b) Der Antriebszapfen muss M3x10 lang sein.
    c) Die Nut in der Stellverstellung ist unnötig.
    d) Markierung an Lehre 2654.99 ergänzt.
    -> 2654 Kh, 2654 Ph und 2658 S.4aL/4bR angepasst.
    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
    [2654 Ph W- und Gsp-Antrieb.dxf, 2658 S.4aLh 1 WAntr 2654+Lehre.dxf, 2658 S.4bRh 1 WAntr 2654+Lehre.dxf]
2026-01-06 265: Weichenantrieb 2654 korr., Demoprojekt für 6 Antriebe
    - Eine weitere Änderung: Das Führungs-Y im
    Drehhebel ist minimal nach innen gelegt, um
    längere Sperr-Hübe zu erreichen.
    - 2658 S.5* für 6 neue Weichenantriebe für
    Demoanlage ergänzt.
    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
    [2654 Ph W- und Gsp-Antrieb.dxf, 2658 S.5aLh 6 WAntr, 4 ZSch.dxf, 2658 S.5bRh 6 WAntr, 4 ZSch.dxf]
2026-01-06 2654: Demoprojekt korrigiert
    - ZProbes in 2654.4-Korrektur ignoriert
    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
    [2658 S.4aLh 1 WAntr 2654+Lehre.dxf]
2026-01-15 3202: Kleine Korrekturen
    - Doppelhebel-Pfade: Radien der Leerrinne korrigiert
    - Doppelhebel-Konstruktion: Tippfehler korrigiert
    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
2026-01-19 265: Korrektur
    - 2654.Kh: Riegelschieber: Ausschnitt um 1,5mm verlängert, damit Zapfen nicht
    an Riegelschieber anschiebt, sondern sich oben anklemmt.
    - 2654.Pv: 15x30x15-Pfade um 1mm verschoben (weil Profil nur so auf Opferplatte passt)
    - 2658.4-Demoprojekt nur Stellverstellung und Bohrlehre korr.fräsen
    - 2658.5-Demoprojekt 15x30x15-Pfade korrekt gelegt
    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
    [2654 Pv W- und Gsp-Antrieb.dxf, 2658 S.4aLh 1 WAntr 2654+Lehre.dxf, 2658 S.5aLh 6 WAntr, 4 ZSch.dxf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]
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2026-02-07 265: Riegelzapfen fräsen, Lehre korrigiert
    - Riegelzapfen 2654.9 wird nun aus Ø6x1 gefräst
    - Lehre 2654.99: Einschnitt für Anstriebszapfen korrigiert
    - Ergänzung in Zv 2654 bei Schrauben für Schiebermontage
    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
    [2654 Pv W- und Gsp-Antrieb.dxf, 2658 S.5aLh 6 WAntr, 4 ZSch.dxf]
2026-02-07 265: Pfad 2654.99 korrigiert
    - Pfad 2654.99P (Rahmenlehre) korrigiert
    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
    [2654 Pv W- und Gsp-Antrieb.dxf]
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2026-04-06 205: Schloss und Schlüssel - Aufspann- & Stücklistenpfad für 5 Schlösser korrigiert
    a. Aufspann- & Stücklistenpfad für 5 Schlösser korrigiert
    b. Unnötige Gruppenpfade entfernt
    - Keine.
    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
    [2052-2053 P.3v Schloss, Schlüssel.dxf, 2058 S.2aLh 5 Schlösser.dxf, 2058 S.2bRh 5 Schlösser.dxf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]
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2026-04-17 380: Update Ausweichwalde
    - GCode für Schlösser neu erzeugt nach Bugfix PathDXF2GCode.
    - Pläne ergänzt
    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
    [3808 S.1h Schlüsselwerk Alu 1.dxf, 3808 S.2h Schlüsselwerk Alu 2.dxf, 3808 S.3h Schlüsselwerk Acryl 1.dxf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]
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2026-04-26 320: Gruppenpfade korrigiert
    - Bei der Gruppenpfaden waren falsche Linienarten
    vorhanden (__ _ _ __ statt _ . _), und bei den
    Pfaden für 5mm-Alu stand falsch T2 statt T5.
    Das ist nun korrigiert.
    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
    [3206 Pv Einzelhebel JE Gruppenpfade.dxf, 3207 Pv Doppelhebel JE Gruppenpfade.dxf, 3208 Pv Einzelhebel JE mit Schl. Gr.pfade.dxf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]
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2026-04-30 2701: Zentralschloss 5701 -> Schlüsselwerk 2701
    - Ganzes Zentralschloss von 5701 nach 2701 Schlüsselwerk
    umgezogen (referenzierde Projekte müssen noch korrigiert
    werden).
    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
    [2701 P.1v Gehäuse, Umlenkungslehre.dxf, 2701 P.2v Gehäuse Acryl.dxf, 2701 P.3v Zentralschlossschieber Länge 1.dxf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]
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2026-05-01 3808: Schlüsselwerk von 570* auf 270* umgezogen, Hebel mit Z-Probes und korr
    - Hebel-Aufspannpfade mit ZProbes versehen.
    - M-Werte für Hebel-Aufspannpfade korrigiert.
    - Schlüsselwerk auf 270*-Pafed umgezogen.
    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
    [3808 S.1h Schlüsselwerk Alu 1.dxf, 3808 S.2h Schlüsselwerk Alu 2.dxf, 3808 S.3h Schlüsselwerk Acryl 1.dxf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]
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2026-05-04 2502.2T: Pfad-Params-Verweis korrigiert
    [2502 Pv Unterzug für zwei Abtriebe.dxf]
2026-05-04 2501.1R: Länge um 0,01 mm korrigiert
    [2501 Pv Unterzug für Einzelhebel.dxf]
2026-05-04 380: Aufspannpfade korrigiert, für Unterzüge erstellt
    - 3808 S.6: Die Fräsung der Rollenrillen soll direkt nach der
    Fräsung der Rollen erfolgen, damit möglichst derselbe
    Nullpunkt verwendet werden kann. Daher habe ich die
    Fräsdurchgang-Reihenfolge geändert: 3808 S.6bT kommt nun
    vor 3808 S.6cR.
    - 3808 S.7: Aufspannpfade erstellt.
    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
    [3808 S.7aLh Unterzüge.dxf, 3808 S.7bTh Unterzüge.dxf, 3808 S.7cRh Unterzüge.dxf]
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2026-05-10 320*: Fehler in Pfaden korrigiert
    - 320*-Pfade waren zum Teil ohne Stützstege oder
    Markierungsfräsungen. Ein Pfad war vollständig
    ohne Befestigung am umliegenden Material - beim
    letzten Loch ist daraufhin der Fräser gebrochen :-(.
    Das sollte nun alles korrigiert sein.
    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
    [3201 Pv Einzelhebel JE.dxf, 3202 Pv Doppelhebel JE.dxf, 3203-3204 Pv Hebel JE mit Schloss.dxf]
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2026-05-24 321*: Korrektur an Pfaden für Hebelabtriebe
    - 3211.5, .8, .9 Lochdurchmesser von 2,5 auf 3 mm korrigiert
    - 3211.7 2 Lochdurchmesser von 3 auf 2,5 mm korrigiert
    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
    [3211 P.1v Hebelbank JE.dxf, 3211 P.3v Hebelbank JE.dxf]
2026-05-24 250*: Hebelabtriebe - Fehler korrigiert
    - 2501.1 Rahmen war spiegelverkehrt, Länge
    um 0,01 mm korrigiert
    - Ergänzungen zu Zusammenbau
    - 3808.*7* Abtriebrahmen-Längen an
    2501.1 angepasst.
    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
    [2500 Pv Hilfspfade, man.Teile für Abtriebe.dxf, 2501 Pv Abtrieb für Einzelhebel.dxf, 2502 Pv Abtrieb für zwei Anlenkungen.dxf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]
2026-05-24 250*: Hebelabtriebe - weitere Fehler korrigiert
    - 2501.3, 2503.2 Schieber mit fehlenden
    Schlitzen versehen
    - Bemaßungen für Schieber und Räder ergänzt
    - Stücklisten für Schauben korrigiert
    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
    [2501 Pv Abtrieb für Einzelhebel.dxf, 2503 Pv Abtrieb für dreistellige Anlenkung.dxf]
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2026-05-31 320*, 321*, 380*: Korrekturen
    - Viele kleinere Probleme korrigiert, die sich
    beim ersten Demoaufbau gezeigt haben;
    - vor allem aber Abstand der Hebelbankträger
    von (außen) 44 auf 40 mm korrigiert.
    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
    [3201 Pv Einzelhebel JE.dxf, 3211 P.1v Hebelbank JE.dxf, 3211 P.2v Hebelbank JE.dxf]
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2026-06-11 2055: Korrekturen an Pfaden
    - Pfadbezeichnung, M korrigiert.
    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
    [2055 Ph Doppelschloss.dxf]
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

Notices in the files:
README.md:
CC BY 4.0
